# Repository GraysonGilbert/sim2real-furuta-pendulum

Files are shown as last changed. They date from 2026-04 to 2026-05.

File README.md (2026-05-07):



# **Robust Control of a Furuta Pendulum: Leveraging PPO and MuJoCo for Sim2Real Transfer**

**ENPM690 Final Project – University of Maryland**

**Team Members:**
* Grayson Gilbert

---
## Table of Contents

1. [Overview](#overview)
2. [Project Sewtup](#project-setup)
3. [Repository Layout](#repository-layout)
4. [Project Workflow](#project-workflow)
   - [Train PPO Model](#1-train-ppo-model)
   - [Evaluate Model](#2-evaluate-model)
   - [Export Policy to Header File](#3-export-policy-to-header-file)
   - [Flash Microcontroller to Run Policy on Hardware](#4-flash-microcontroller-to-run-policy-on-hardware)
5. [Hardware Components](#hardware-components)
5. [License](#license)

## **Overview**
This project bridges the gap between high-fidelity physics based simulation and physical hardware by developing a robust Proximal Policy Optimization (PPO) based controller for a furuta pendulum. The project trains an agent that can repeatedly swing up and balance a pendulum, while handling the noise, friction, and non-linearities of the real world. This was achieved through simulation using MuJoCo before being transferred to an ESP32 onboard the physical furuta pendulum. The resulting model is capable of balancing a pendulum for over an hour continuously (upper limit not found), and is robust to external input forces.

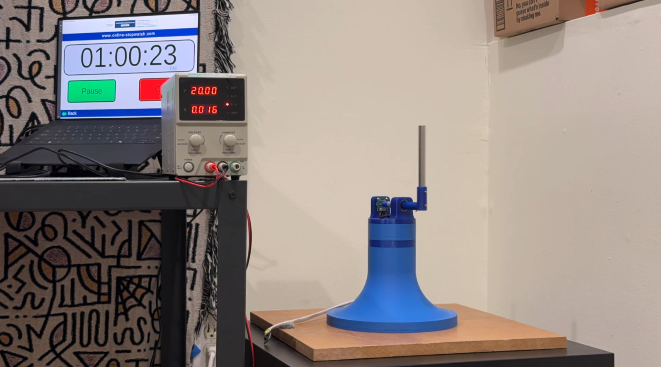
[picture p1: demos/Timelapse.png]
Description


---

## **Repository Layout**

```
sim2real-furuta_pendulum/
├── demos/                     # Project demonstration pictures and videos
├── envs/                      # Custom Gymnasium training environment
├── hardware/                  # Arduino sketch to control ESP32 and Solidworks assembly
├── rl/
│   ├── exported_models/       # Exported PPO model weight header files
│   ├── logs/                  # Model training Tensorboard logs
│   ├── saved_models/          # Automatically saved PPO models
├── sim/                    
│   ├── hw_sim_debug/          # Model and hardware related debug csv files
│   ├── meshes/                # Pendulum CAD meshes
│   ├── models/                # Pendulum MuJoCo model
├── utils/                     # All python scripts necessary for model viewing, training, evaluation, and debug
├── README.md                  # This file
├── requirements.txt           # Prerequistes
├── Dockerfile                 # Builds project docker container    
```

---
## **Project Setup**

### **Setup via Docker Container**

Download the ```Dockerfile``` from this repository and navigate to its saved location. Then run the following commands:

**Note: The docker container can be built with Nvidia GPU acceleration if the host machine has the available Nvidia hardware. This is the default configuration. If the host machine does not have the required Nvidia GPU, the Dockerfile can be modified for CPU processing only. Follow instructions inside the Dockerfile to modify the file for CPU only processing.**

#### GPU Accelerated Docker Container Setup
```shell
# Build Dockerfile image with 
docker build -t furuta-sim-env .
```

```shell
# Nvidia GPU accelerated docker container
#
# Create docker container from image [Deletes container after exit]
xhost +local:docker
docker run -it --rm \
    --gpus all \
    --device /dev/dri:/dev/dri \
    --net=host \
    -e DISPLAY=$DISPLAY \
    -v /tmp/.X11-unix:/tmp/.X11-unix \
    -v $HOME/.Xauthority:/root/.Xauthority \
    -e MUJOCO_GL=glfw \
    -e __NV_PRIME_RENDER_OFFLOAD=1 \
    -e __GLX_VENDOR_LIBRARY_NAME=nvidia \
    furuta-sim-env bash

# Nvidia GPU accelerated docker container
#
# Create docker container from image [Keeps container after exit]
xhost +local:docker
docker run -it \
    --name=mujoco-container
    --gpus all \
    --device /dev/dri:/dev/dri \
    --net=host \
    -e DISPLAY=$DISPLAY \
    -v /tmp/.X11-unix:/tmp/.X11-unix \
    -v $HOME/.Xauthority:/root/.Xauthority \
    -e MUJOCO_GL=glfw \
    -e __NV_PRIME_RENDER_OFFLOAD=1 \
    -e __GLX_VENDOR_LIBRARY_NAME=nvidia \
    furuta-sim-env bash
```

#### CPU Only Docker Container Setup:
```shell
# Buid dockerfile with
docker build -t furuta-sim-env-cpu-only .
```
```shell
### CPU only mode
xhost +local:docker
docker run -it --rm \
    --net=host \
    -e DISPLAY=$DISPLAY \
    -v /tmp/.X11-unix:/tmp/.X11-unix \
    -v $HOME/.Xauthority:/root/.Xauthority \
    -e MUJOCO_GL=glfw \
    furuta-sim-env-cpu /bin/bash
```

### **Setup via Cloning Repo**
```shell
# Clone the repository
git clone https://github.com/GraysonGilbert/sim2real-furuta-pendulum.git
```
---

## **Project Workflow**

### **1. Train PPO Model**
* The first step in the project workflow is training the PPO model to swing up and balance the pendulum. Run the following ```train.py``` script to launch the multi-core cpu based model training.

```shell
# From the sim2real-furuta-pendulum directory navigate to utils/
cd utils/
```

```shell
# Kick off training for PPO model
# 
# NOTE: The training script was designed around the Intel(R) Core(TM) Ultra 7 155H CPU.
#       It is reccomended to spread across 10 cpus cores if available. Default option
#       is set to single core training.
#
# Use --help for information about the various CLI arguments

python3 train.py --mode swing_up --num_cpus 10 # Note 10 cores specified

```

```shell
# View Tensorboard logs in a browser while training a model
#
# In a separate terminal (if running in container, terminal must be in a container as well) run the following
# from the sim2real-furuta-pendulum/ directory

tensorboard --logdir ./rl/logs/
```

### **2. Evaluate Model**

* Evaluate the results of the trained model in the MuJoCo simulation using the following ```evaluate.py``` script. This will the launch a single instance of the MuJoCo model viewer, controlled by a specified model.
```shell
# Evaluate trained policy on MuJoCo model
#
# Default values will run example simualtion on a pre-trained swing up policy
#
# Use --help for information about the various CLI arguments

 python3 evaluate.py --mode swing_up --model_name <Model name saved under /saved_models>
 
 # Example:  python3 evaluate.py --mode swing_up --model_name /swing_up_1777060502/ppo_furuta_swing_up_14000000_steps.zip
```

### **3. Export Policy to Header File**

* The next step will be to convert the resulting trained policy into source code capable of running on memory constrained devices such as an esp32. Use the following command to run a script that converts the trained PPO policy into source code.
```shell
# Export the trained policy weight into a C++ header file for running on embedded devices
#
# NOTE: The model_name argument assumes the model is within the /rl/saved_models/ direcotry
#
# Use --help for information about the various CLI arguments

python3 export_to_cpp.py --model_name <model_name_goes_here> --output <policy_name_goes_here> # Default filename is policy_net.h
```

### **4. Flash Microcontroller to Run Policy on Hardware**
* **Note: Configuring and setting up the esp32 device for use with the Arduino IDE is outside the scope of this project.**
* Move file into your local Arduino directory where libraries are stored. This will allow the ```policy_net.h``` file to be discoverable when compiling the arduino sketch. Copy over ```esp32_PPO_furuta_balancer.ino``` into an Arduino IDE for flashing onto the esp32.

---

## **Hardware Components**

* iPower GM4108h-120T Brushless Gimbal Motor
* CUI Devices AMT103V ABI Encoder
* I2C Bi-directional 3.3V-5V Level Shifter
* ESP32 Lolin Lite Development Board
* DENG FOC V3 Brushless Driver Board
* AS5047P SPI Magnetic Rotary Encoder
* 3D Printed Pendulum Parts
* 304 Stainless Steel Rods for Pendulum Mass

The full Solidworks assembly is available under the ```hardware/``` directory.

---

## **License**

This project is licensed under the **MIT License**.

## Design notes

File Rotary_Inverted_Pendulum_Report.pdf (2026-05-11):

Grayson Gilbert
ENPM690
Final Project Report

# Robust Control of a Furuta Pendulum:

## Leveraging PPO and MuJoCo for Sim2Real Transfer

## Abstract:

This project demonstrates the successful zero-shot sim2real transfer of a deep reinforcement learning policy for the robust control of a furuta pendulum. The furuta pendulum, a highly non-linear, 2-Degree of Freedom (DoF) underactuated robotic system, presents a complex continuous control challenge due to real-world friction, sensor noise, and communication latency. To effectively bridge the simulation-to-reality gap, a high-fidelity MuJoCo physics simulation was developed and meticulously calibrated against physical hardware responses using isolated drop and rotor tests. A Proximal Policy Optimization (PPO) agent was trained within a custom Gymnasium environment that utilized a multi-phase curriculum learning reward structure to sequentially teach swing-up and balancing behaviors. To ensure policy robustness upon deployment, the training environment heavily incorporated domain randomization, manual velocity noise injection, and action latency buffers. The finalized model weights were deployed directly to an ESP32 microcontroller leveraging Torque Field Oriented Control (FOC), requiring absolutely no further tuning or training on the physical hardware. The physical system successfully executed the swing-up maneuver and maintained an active balance for over a continuous hour during endurance testing. Ultimately, this work highlights the efficacy of combining accurately grounded physics simulations with robust reinforcement learning strategies to overcome the sim2real gap in complex, underactuated physical systems.

## Project Goal/Introduction:

The goal for this project is to bridge the gap between high-fidelity physics based simulation and physical hardware by developing a robust Proximal Policy Optimization (PPO) based controller for a furuta pendulum. The project aims to train an agent that can repeatedly swing up and balance a furuta pendulum, while handling the noise, friction, and non-linearities of the real world.

The furuta pendulum, also known as the rotary inverted pendulum, is a classic 2 Degrees of Freedom (DoF) underactuated control problem. It is composed of a single, powered, rotating base, attached to a free-spinning unpowered pendulum mass.

An example of a furuta pendulum controlled via classical control methods can be found by clicking the following link: Furuta Pendulum Example Video (https://youtu.be/XKzzWe15DEw?si=Pk6LUR-PZWryq1gJ)

## Literature Survey:

Proximal Policy Optimization (PPO) in Continuous Control: Deep reinforcement learning (RL) has quickly become the go-to approach for continuous control tasks in robotics. For this project, Proximal Policy Optimization (PPO) was selected because it strikes an excellent balance between sample efficiency and training stability. Research shows that PPO improves upon earlier Trust Region Policy Optimization (TRPO) methods by utilizing a clipped surrogate objective. This clipping mechanism prevents the model from making excessively large policy updates during training. As a result, it maintains performance guarantees while significantly reducing computational overhead, making it highly effective for the high-frequency 100Hz control loops required when running on the physical microcontroller.

Reinforcement Learning for the Furuta Pendulum: The Furuta pendulum is characterized by highly non-linear dynamics driven by gravity, Coriolis, and centripetal forces. Traditionally, controlling this system required complex analytical derivations and heavy simplifications of physical laws to keep the pendulum in an inverse equilibrium state. However, recent advancements demonstrate that RL algorithms can successfully bypass these explicit rigid-body modeling constraints. By allowing the agent to learn adaptive control policies directly within high-fidelity physics simulators, like MuJoCo, stable policies can be developed rapidly without the temporal or spatial constraints of training on physical hardware.

Bridging the Sim2Real Gap through Robust Control: While simulation environments allow for rapid and safe policy exploration, transferring these trained policies to the real world remains the largest hurdle. Optimal policies generated in pure simulation frequently overfit to the approximated dynamics and fail when exposed to real-world uncertainties like sensor noise, communication latency, and unmodeled friction. Robust reinforcement learning addresses this fragility by explicitly accounting for these uncertainties during the training phase. By introducing external disturbances and randomizing physical parameters (like mass, motor torque, and damping) within the training environment, the agent is forced to learn resilient recovery behaviors. This approach yields policies that are significantly more robust against physical mass changes and non-ideal actuators.

Summary and Research Implications: Overall, the literature confirms that while model-free RL algorithms like PPO are highly capable of generating successful policies for underactuated systems, raw sim-trained models are inherently brittle upon physical deployment. Overcoming this sim2real gap requires the explicit integration of robust RL techniques like domain randomization, noise injection, and structured curriculum learning. These foundational findings directly informed the methodology of this project, justifying the design of the custom Gymnasium environment to ensure the PPO agent learns predictive, robust control capable of seamless transfer to the physical system.

## Hardware:

### Component Breakdown:

- 3D Printed Pendulum Parts (base, pendulum support, and other various components)
- 1x iPower GM4108H-120T Brushless Gimbal Motor
- 1x 8mm slip ring
- 1x CUI Devices AMT103V ABI Encoder
- 1x I2C Bi-directional 3.3V-5V Level Shifter
- 1x ESP32 Lolin Lite Development Board
- 1x DENG FOC V3 Brushless Driver Board
- 1x Push-button Switch Development Board
- 1x AS5047P SPI Magnetic Rotary Encoder
- 2x 304 Stainless Steel Rods for Pendulum Mass
- 1x Benchtop Power Supply

### CAD Model:

The 3D model was originally developed using Solidworks. Each individual model was designed from scratch, except for the AS5047P encoder, which was provided by the board manufacturer. Once the individual components were complete, the entire system was assembled, and constrained accordingly. It is important to note that at this step all component frames must be aligned appropriately before exporting the model for simulation. Failure to do so will result in misaligned parts and unexpected responses from the simulated physics engine. An exploded view of the exported assembly can be found below. In an effort to simplify the model during simulation, non-essential electronic components were removed from the assembly.

Exploded View Diagram:
1. PLA Pendulum Base - bottom
2. PLA Pendulum Base - middle
3. PLA Pendulum Base - top
4. BLDC Stator
5. BLDC Rotor
6. Rotating Pendulum Support
7. Ball Bearing
8. AS5047P SPI Encoder
9. Diametric Magnet
10. Magnet Holder
11. 8mm SS Rod
12. Pendulum Rod Holder
13. 12mm SS Rod

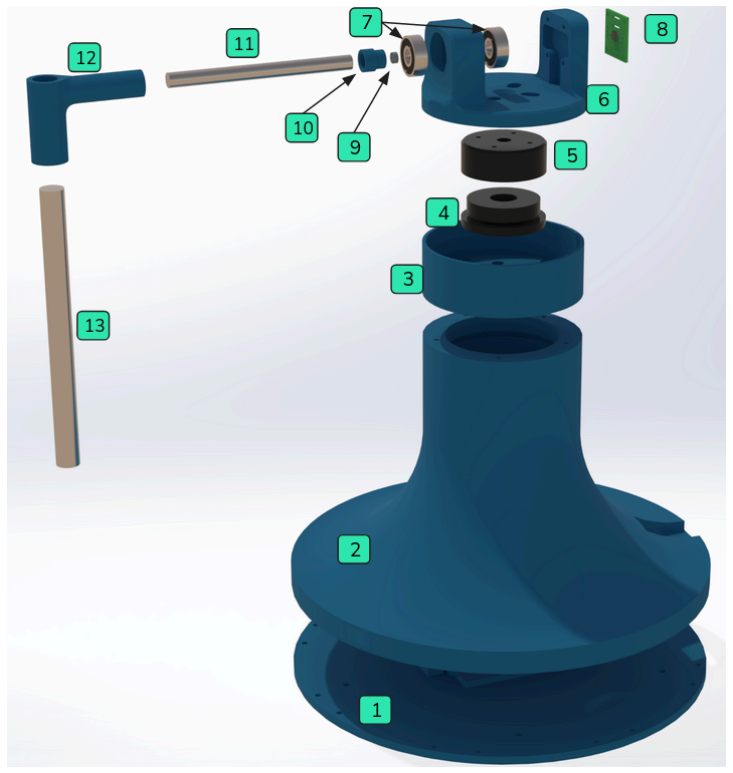
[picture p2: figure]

Exploded view of pendulum assembly.

## Model Simulation:

### Platform:

The pendulum model was then exported to the MuJoCo physics engine for simulation. MuJoCo stands for Multi-Joint Dynamics with Contact, and it is an open-source physics engine developed by Google Deepmind. MuJoCo was selected due to its performance, accuracy, and lightweight nature allowing for high-fidelity simulation on my host machine. Other notable features that aided in the selection of this platform include domain randomization during training, high-frequency training while maintaining a constant control loop rate, and mechanical fidelity between joints and components. These features allow for an accurate simulation of the furuta pendulum without the need for expensive industrial grade GPUs.

### Model Setup:

Once the Solidworks assembly was complete, it needed to be exported into a format MuJoCo can work with. Solidworks is unable to export assemblies in the MuJoCo native MJCF format, however it can export files as a URDF (Unified Robot Description Format). A python script was then developed to convert the URDF to the MJCF for processing in MuJoCo. The base model exported from Solidworks contains the 3D meshes, joints, and links necessary for simple simulation, but it lacks many of the details needed for the realistic physics based simulation.

After the base model was successfully imported into MuJoCo, system specific information was added to the model to ground the simulation in reality.

Notable motor specifications were pulled directly from the manufacturer’s website linked here. (https://shop.iflight.com/ipower-motor-gm4108h-120t-brushless-gimbal-motor-pro217)

No-load Voltage: 20V
No-load RPM: 513-567RPM [540RPM avg]
Load Voltage: 20V
Load current: 1.5A

From these specifications the following information about the motor can be calculated:

Kv (Motor Velocity Constant) = No-load RPM / No-load Voltage = 540/20 = 27
Torque constant = 8.27 / Kv = 8.27 / 27 = 0.306 Nm/A

The load current defines the control range of the actuator to [-1.5A, 1.5A], and the torque constant (0.306) is directly applied to the actuator gear value in the MuJoCo model. Additionally, position and velocity sensors at the rotor and pendulum joint were defined to replicate the physical system hardware.

After the physical motor parameters were established, the remaining simulation parameters were tuned to match the physical system response. First, an isolated pendulum drop test was performed. The rotor of the BLDC was fixed in place to completely isolate the pendulum motion. The pendulum was raised to be 90 degrees from the bottom resting position. At this point a data collection logger was started to record pendulum position over time. The pendulum was released from the horizontal position and allowed to oscillate back and forth until coming to a complete stop. The experiment was repeated in the MuJoCo simulation and the results were compared.

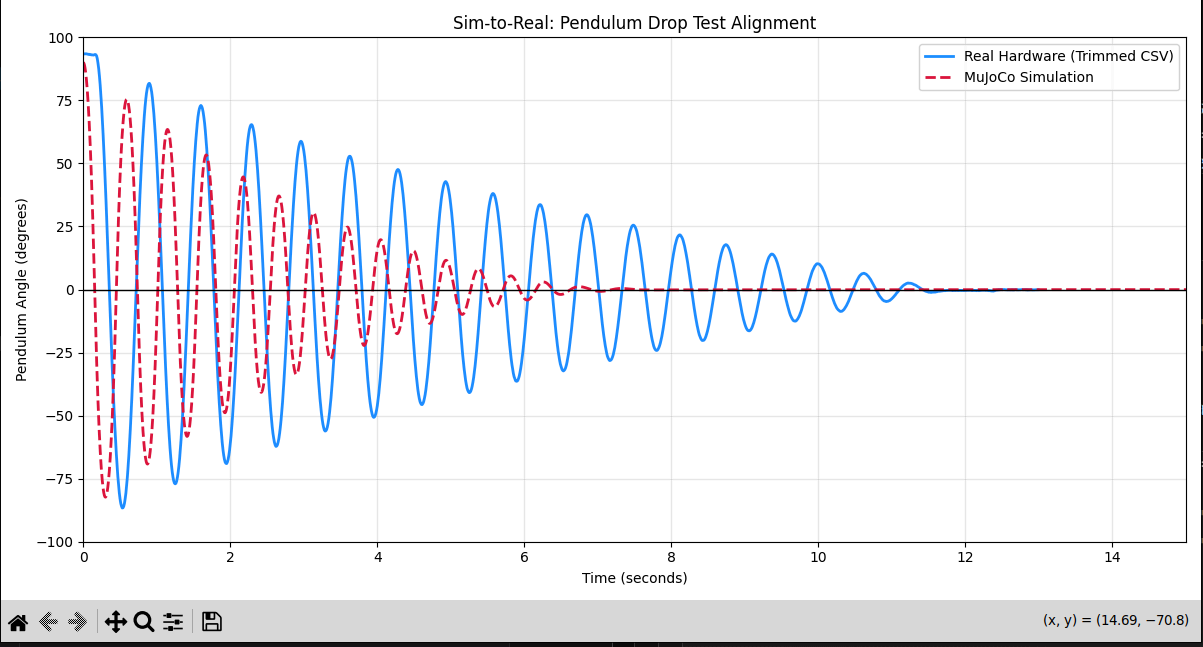
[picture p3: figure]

Initial pendulum drop test response.

The initial pendulum drop test showed that phase of the simulated pendulum oscillations did not match the physical system. This was likely due to the simulated center of gravity differing from the real system. To resolve this, I modified the pendulum center of mass location in the MuJoCo model until the phase was better aligned with the real system. The damping and friction loss parameters were also tuned until the simulated pendulum nearly matched the physical response shown below.

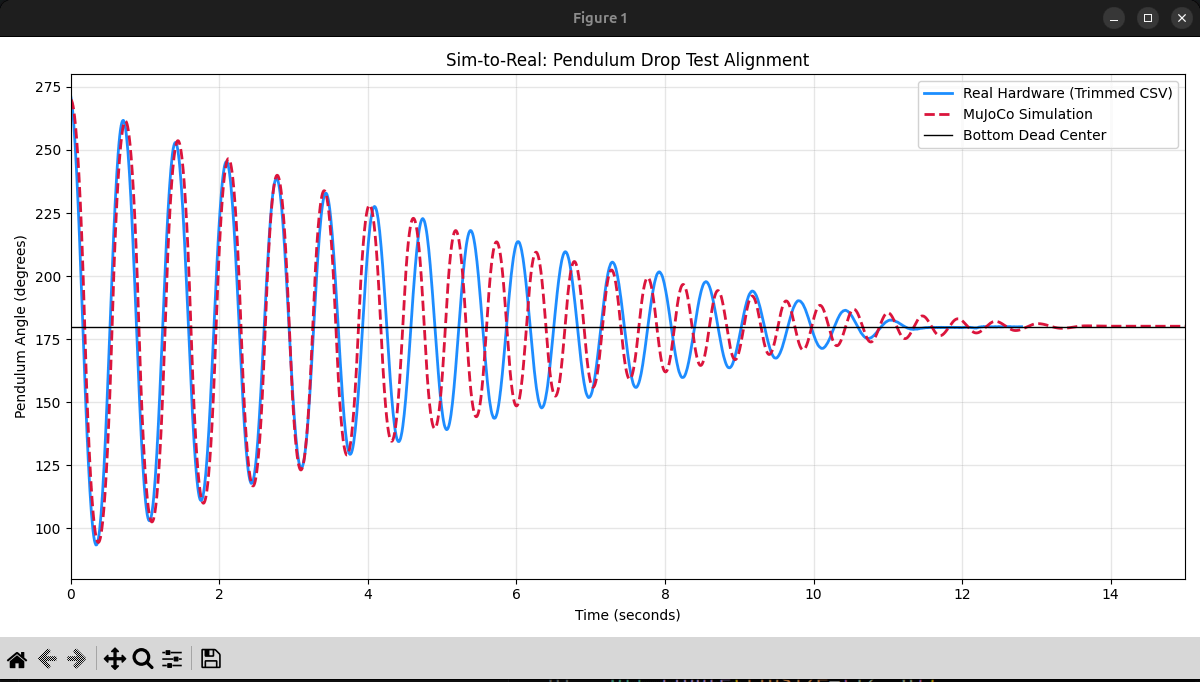
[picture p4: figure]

Final pendulum drop test response.

After the pendulum simulated response matched the physical system, the rotor isolation test was performed. For this test the pendulum was fixed in the bottom position, and the rotor was commanded to spin at constant rate. Like the first test, a logging script was deployed to record system data. The rotor isolation test started the motor from 0 rad/s and accelerated it until it reached a steady 20 rad/s. This velocity was held constant for 5 seconds before the motor commands were stopped and the rotor was allowed to coast until it came to rest. The same experiment was repeated in the simulation and the initial test results are shown below. Please note that for this initial experiment, the pendulum was not constrained appropriately resulting in noisier readings, and a different initial response than in the final tests.

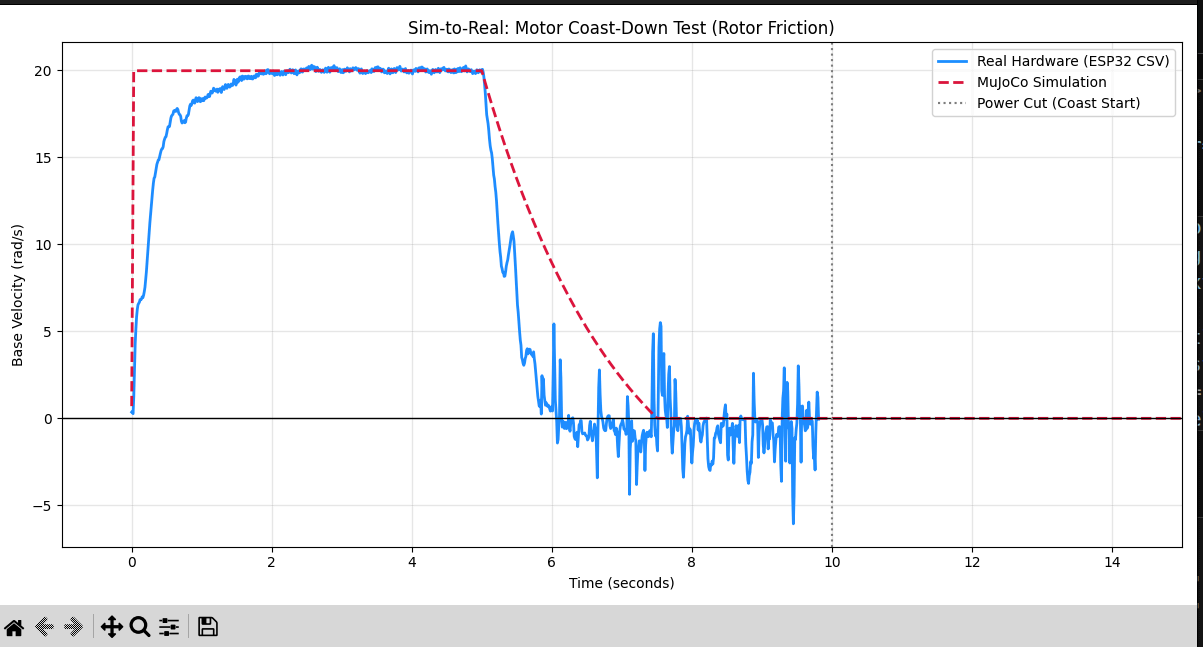
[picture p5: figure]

Initial rotor isolation test response.

After conducting the initial rotor isolation tests, the friction loss and damping values were once again tuned until the simulation better aligned with the physical system response. The final rotor isolation response is shown below.

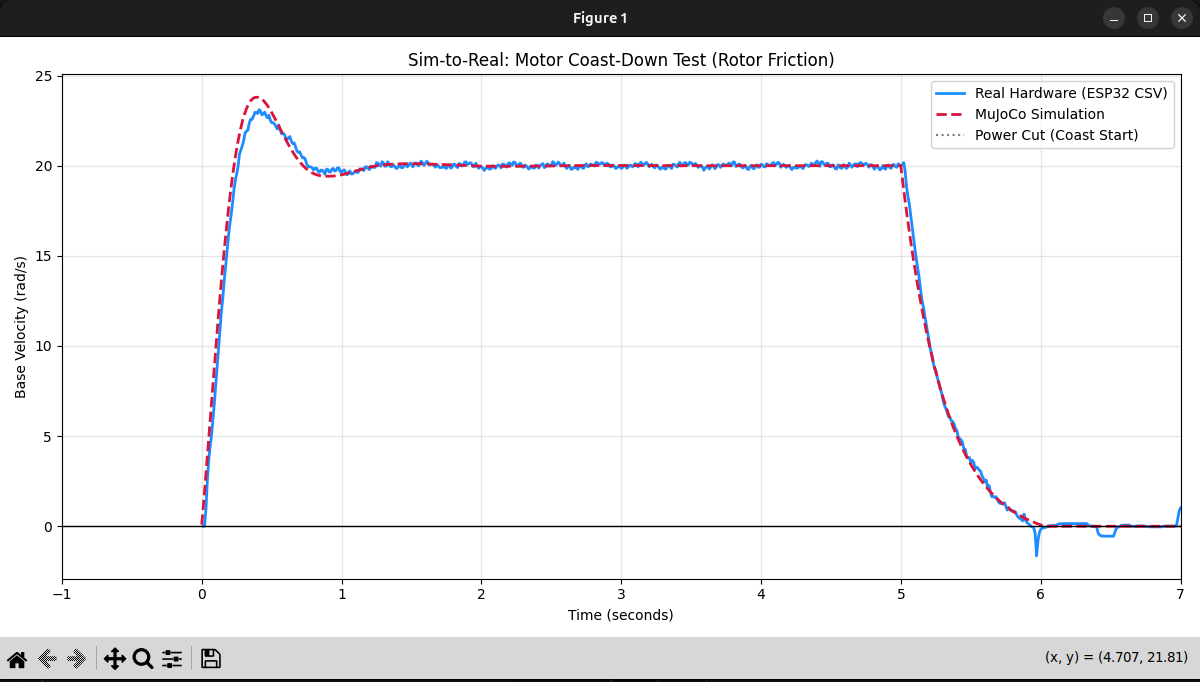
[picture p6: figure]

Final rotor isolation test response.

At this point the MuJoCo model was grounded in physics, and the simulated pendulum system response was nearly identical to the physical pendulum system. The model was now ready for the next step, which was creating the environment for training.

### Environment Setup:

With the MuJoCo model ready for training, the next step was to create the simulation environment for reinforcement learning. To achieve this, I wrapped the MuJoCo model in a custom Gymnasium environment. Gymnasium is a reinforcement learning API that bridges the gap between the MuJoCo physics engine and the RL algorithm. The environment consists of the following functions: initialize, step, observe, terminate, reset, and reward.

Initialize:
The environment initializes by first loading in the MuJoCo model data. After this, it will define a frame skip variable and set it equal to 10. The frame skip is used to mimic the real world 100Hz control loop that runs on the microcontroller. A frame skip of 10 results in a control loop rate of 100Hz because the MuJoCo model timestep is 0.001 seconds. After the frame skip is defined, physical hardware limits like motor current and encoder resolution are set. Then the 1 dimensional action space is initialized and constrained to the range of [-1, 1]. For this environment, the action space is the commanded motor current. Next, the 6 dimensional observation space is defined and constrained to the range of [-1, 1]. Various model parameters like motor torque constant, model damping, model friction, and model mass are then initialized for future domain randomization in the reset function. Finally, the action delay buffer is initialized to mimic real life communication latency.

Step:
This function is also known as the execution loop for the RL environment. The simulation step takes the model action as a parameter, in this case the commanded motor current. Because the action is constrained to a range of [-1, 1], it is multiplied by the maximum motor current to scale the action into physical amps. Next the action is added to the delay buffer so it does not get applied immediately. Instead the model must wait a couple steps before the action is applied. This buffer mimics the real life communication latency in the system, and forces the model to learn predictive control instead of relying on instantaneous response times. Then, the commanded current for this given step is applied for the next 10 frames. This is how the frame skip is implemented, and sets the 100Hz control rate. After the frame skips are complete, the raw position and velocity data for the motor and pendulum are read from the model. The pendulum position is then wrapped between the values of [-pi, pi], and the raw system state is generated. The observation function is called using this raw state as an input, followed by the reward function. Next, the previous target current is updated to be the current target current, and the termination function is checked to see if termination criteria are met. If the simulation is to be terminated, the type of termination is logged for telemetry. Finally, the observation, reward, termination, and telemetry values are returned.

Observation:
The observation function takes the raw system state as an input parameter. The raw state includes rotor position, rotor velocity, wrapped pendulum position, and pendulum velocity. Then the raw state positions are quantized into acceptable values within the encoder resolution. Next, noise is manually injected into the velocity sensor readings. This noise is added because of the way the physical system calculates the pendulum and rotor velocity. In the real system, the velocity is calculated by taking the derivative of the encoder position. These sensor readings are inherently noisy, which can have a large impact on overall velocity when the motor or pendulum is moving at slow speeds. The simulation sensors do not automatically have noise in their readings, so it must be injected manually. Next the maximum rotor position, maximum rotor velocity, and maximum pendulum velocity are defined. These values are used in the following observation array to keep the velocity and position values between the range [-1, 1]. The observation space array includes the following values:
1. Discrete rotor position / maximum rotor positon
2. Noisy rotor velocity / maximum rotor velocity
3. Sine component of discrete pendulum position
4. Cosine component of discrete pendulum position
5. Noisy pendulum velocity / maximum pendulum velocity
6. Previous commanded current / maximum commanded current

The pendulum position is broken down in its sine and cosine components as a way to prevent sudden value jumps when the pendulum wraps around the maximum position. These sudden jumps in value would otherwise confuse the RL model during training, resulting in poor performance.

Reset:
The simulation reset occurs when training starts, or when termination criteria are met. The reset function completely resets the training environment, preparing it for the next episode of training. The pendulum environment contains two potential training modes that affect the system reset. The training modes are Balance and Swing Up. The Balance mode resets the pendulum environment and initializes the pendulum near the Top Dead Center (TDC) position. This is the upright, unstable position. The Swing Up mode resets the pendulum environment and initializes the pendulum in the Bottom Dead Center (BDC) position. Both training modes also incorporate domain randomization. This means that the simulation randomizes the values for motor torque, model friction, model damping, and model mass within a specified range. This domain randomization helps to improve overall model performance and robustness.

The various training modes are a result of curriculum learning. For more information about the curriculum learning process please see the Reward function section below.

Termination:
The termination criteria for the simulation episode is based on the mode of the training being conducted. If any of these criteria are met during a training episode, the simulation will immediately stop the episode, log the termination type, and reset the environment.

The termination criteria for the Balance training mode is the following:
- The pendulum drops below 15 degrees away from the TDC position
- The motor spins more than 2 full rotations in any one direction

The termination criteria for the Swing Up training mode is the following:
- The motor spins more than 2 full rotations in any one direction

Reward:
The reward function is the most important part of the training environment. Without an appropriately designed reward, the model will not be able to learn the desired task. Swinging the pendulum from the BDC position, and then catching and balancing it in the TDC position is not trivial. It would be very difficult to design a reward function that can achieve this system response without breaking it up into smaller parts. This is where curriculum learning comes into play. Instead of starting model training by attempting difficult and complex tasks, the curriculum learning approach breaks the complex problem down into smaller more manageable tasks. The agent is taught to successfully complete the smaller, easier tasks before learning more challenging operations. This approach is very similar to how students first learn basic arithmetic before tackling harder concepts like calculus.

With this in mind, the pendulum problem was broken down into two main sub-tasks: 1. Swing up the pendulum 2. Catch and balance the pendulum. The second task was the easier of the two so that is where the training started. The model learned to stabilize the pendulum in the upright position using the Balance training mode. Each episode reset the pendulum near the TDC position allowing for the model to have millions of opportunities to learn to balance the unstable mass. Once the reward was designed in a way that enabled the model to successfully balance the pendulum, the swing up task was taught. The swing up task was trained using the Swing Up mode. It built upon the current reward structure to successfully generate momentum to swing the pendulum from the BDC position up to TDC and balance it there for extended periods of time. The final reward function was broken down into two distinct phases based on pendulum position with a third transition phase blending everything together.

The overall reward function is made up of a variety of rewards, bonuses, and penalties. A high level overview of all the rewards, bonuses, and penalties are as follows:

- Upright reward = cos( pendulum position ) - 1
- Effort penalty = 0.001 * ( current ** 2 )
- Centering penalty = 0.03 * ( rotor position ** 2 )
- Action rate penalty = 0.5 * ( ( current -previous current ) ** 2 )
- Rotor velocity penalty = 0.05 * ( rotor velocity ** 2 )
- Catch velocity penalty = 0.02 * ( pendulum velocity ** 2 ) + 0.05 * ( rotor velocity ** 2 )
- Momentum bonus = 0.1 * abs( pend. Velocity ), values clipped between [0.0, 0.8]
- Swing weight = 1.0 - catch weight
- Blended Momentum Bonus = momentum bonus * swing weight
- Blended Velocity Penalty = ( swing base velocity penalty * swing weight ) - ( catch velocity penalty * catch weight )
- Catch Bonus = 3.0 if catch weight == 1.0, otherwise 0
- Duration Bonus = 0.01 * consecutive upright steps

The total reward is defined at the sum of all rewards and bonuses minus the sum of all penalties.

Swing Up Phase Reward Structure:
In the Swing Up phase, reward structure promotes generating pendulum momentum, in order to eventually swing the pendulum up to the TDC position. The pendulum is in the phase any time the pendulum position is greater than 0.6 rads away from TDC. The Swing Up phase reward structure is the following:
- Catch weight = 0
- Swing weight = 1
- Blended momentum bonus -> has full momentum bonus effect
- Blended velocity penalty -> only swing base velocity penalty, no catch penalties
- Catch bonus = 0

- Consecutive upright steps = 0
- Duration bonus = 0

Transition Phase Reward Structure:
The distance between 0.6 rads away from TDC and 0.2 rad away from TDC is considered the transition phase of the reward structure. This space is where both the Swing Up and Balance phases blend together to smoothly transition from one reward structure to the next. The transition phase also helps to slow down the pendulum momentum generated in the Swing Up phase so the pendulum does not carry over the TDC position and swing back towards the BDC position. The transition phase reward structure is as follows:
- Catch weight = (1.2 - distance from TDC) / 1
- Swing weight = less than 1
- Blended momentum bonus -> has reduced momentum bonus effect
- Blended velocity penalty -> contains some swing base velocity penalty and some catch penalties
- Catch bonus = 0
- Consecutive upright steps = 0
- Duration bonus = 0

Catch and Balance Phase Reward Structure:
When the pendulum position is less than 0.2 rads from TDC the Catch and Balance reward phase kicks in. Here the reward heavily promotes keeping the pendulum in this upright position as close to TDC as possible. The Catch and Balance reward structure is as follows:
- Catch weight = 1
- Swing weight = 0
- Blended momentum bonus = 0
- Blended velocity penalty -> swing base velocity penalty + catch velocity penalty
- Catch bonus = 3
- Consecutive upright steps -> +1 for each consecutive step in this phase
- Duration bonus -> greater than 0, and increasing
These different phases of a single reward function allow for one model to be able to learn multiple unique tasks in order to achieve the goal of swinging up, catching, and balancing the pendulum in an unstable position.

Logging:
Throughout the entire simulation process, the observation space of the simulated pendulum is logged. This allows for detailed evaluation and comparison of the simulated and physical pendulum system.

## Reinforcement Learning:

### Algorithm/Approach:

The control strategy relies on Proximal Policy Optimization (PPO), a stochastic policy gradient method chosen for its balance of sample efficiency and stability in continuous action spaces. The overall training pipeline is divided into three distinct phases to maximize the likelihood of success when transferring to real hardware: 1. Initial policy optimization using PPO 2. Improving robustness through randomization 3. Hardware deployment and validation.

The Initial policy optimization using PPO is where the model will learn to swing up and balance the pendulum, with a reward function that promotes smooth motor torque and extended pendulum balance times. The second phase is where the model will incorporate noise into the sensors, latency in motor response time, and changes in physical constants such as mass , motor torque, damping, and friction. This will force the model to create a control response that can withstand the randomness that is the real world. The final phase will be deploying the model on the hardware and validating its effectiveness through balancing the pendulum.

### Training Architecture:

The training program leverages Stable Baseline 3, an open-source python library that provides reliable implementations of the Deep Reinforcement Learning algorithms using the PyTorch framework. More specifically, the training program uses the PPO model built into SB3. The training can be initialized using one of two modes, the Balance mode or the Swing Up mode. Each mode corresponds to the initial environment conditions described in the custom gymnasium environment above. When training is initialized, it will start 10 parallel processing instances of the pendulum model. Parallelizing the model training enables significantly more training capacity without increasing overall training time. The training program also leverages SB3’s extensive logging capabilities with Tensorboard. In addition to the built in logging features, a custom termination callback was implemented to track the number of each termination type as the training evolves. These logging features allow for model evaluation without seeing the simulated system response of the pendulum model. For periodic model evaluation, the training program saves checkpoint policies every 10,000,000 steps to get a better understanding of how the agent is learning without stopping training completely. A single training episode can have a maximum of 1000 timesteps before restarting. This helps to prevent the model from wasting time learning ineffective strategies. The training will proceed for a total of 30,000,000 steps split amongst all parallel instances before saving the final model policy.

Model Hyperparameters:
- Learning rate: 0.0003
- Number steps: 2048

- Batch size: 2048
- Number epochs: 10
- Entropy coefficient: 0.03
- Clip range: 0.2

## Simulation Results:

Following the completion of model training on the pendulum simulation, the model was able to successfully swing up and balance the pendulum in the TDC position. A recording of the simulation in action can be found below:

Simulation Demonstration (https://drive.google.com/file/d/1TTlGVXxSfAPoyIrrarF8xxBkDhk0gaSO/view?usp=sharing)

Below are screenshots of the Tensorboard logs saved from the simulation training process. The first 4 charts are the logs that were most frequently used when evaluating the success of a model during training. Starting from the top left, the base drift termination chart plots how frequently the simulation ended prematurely due to the base drift termination criteria. The next chart shows the pendulum drop criteria. The Swing Up training mode was performed for this simulation, so pendulum drop criteria is ignored. The next chart shows the average reward of a simulation. The reward initially started out very negative as the pendulum was heavily penalized for improper control of the pendulum. As the model learned to generate momentum to swing the pendulum, the reward function slowly increased until it reached 0. When the model finally caught and balanced the pendulum for the first time, the reward sharply increased to the +6000 range where it remained for the rest of the simulation. The top right chart shows the average length of a simulation episode. Each episode can have a maximum of 1000 timesteps before termination. A successful simulation should be able to reach the maximum simulation timestep without terminating. As you can see, this simulation approached the maximum 1000 timestep limit once the model learned to balance the pendulum successfully.

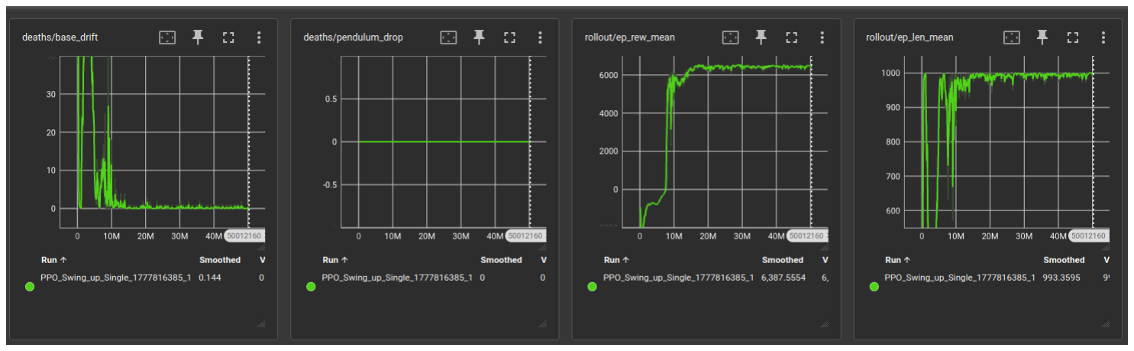
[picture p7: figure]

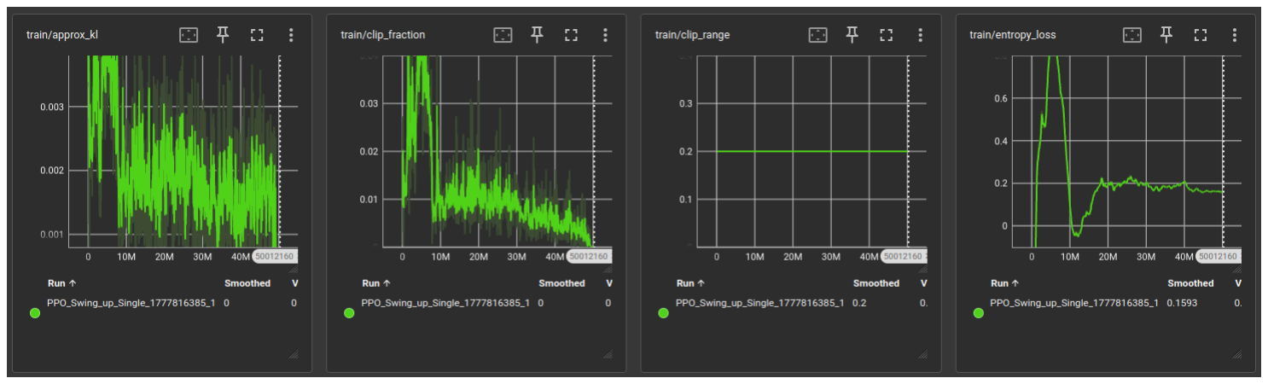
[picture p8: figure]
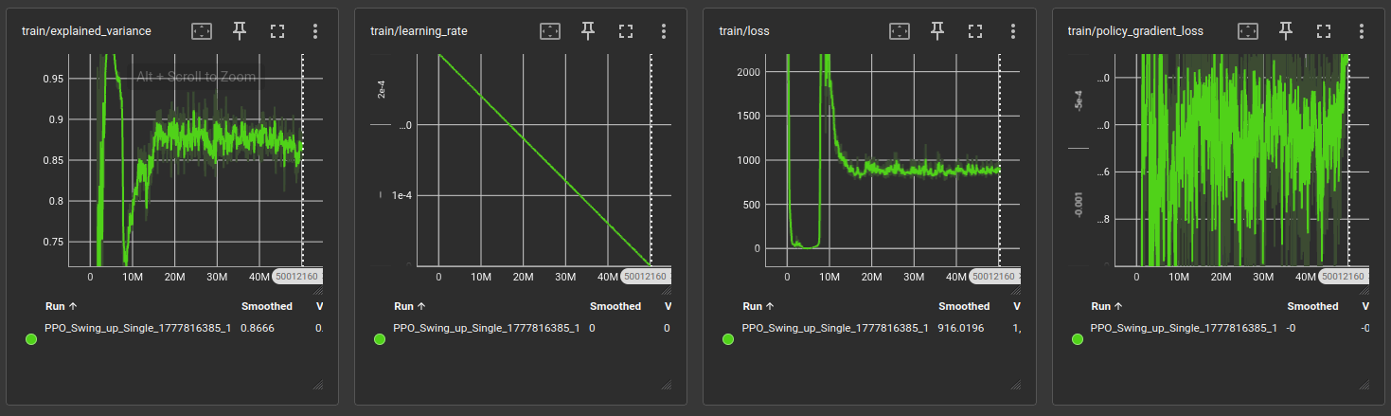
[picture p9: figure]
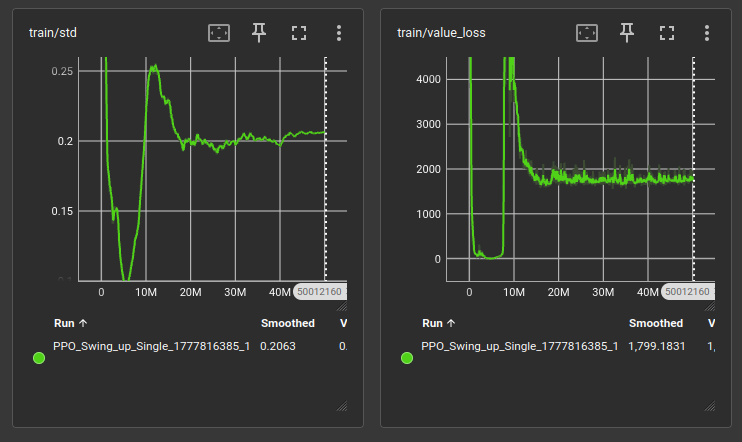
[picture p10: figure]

Tensorboard logging charts for model evaluation.

## Embedded Software:

### Software Architecture:

Once the simulation was successful, the process of transitioning the model onto an embedded device could take place. A completed simulation outputs the trained model in a zip file containing JSON data files, PyTorch variable files, policy files, and policy optimizer files. This zip file cannot directly run on an embedded device. Instead the trained policy weights needed to be exported into a C++ header file, so they can be compiled into the machine code running on the ESP32.

The embedded software architecture utilized both processing cores in the ESP32 microcontroller. Core 0 handled all RL processing related tasks. This core read in the pendulum observation space and calculated the required target current using the exported model weights. This control loop was fixed at the planned 100Hz rate to ensure that the commanded current was received when the model expected it. Core 1 handled all the motor control commands. The brushless motor that drives the pendulum system is controlled using Torque Field Oriented Control (FOC) via current sensing. FOC is a high performance control technique for driving Brushless DC motors (BLDC). It allows the motor to be controlled with extreme precision. The FOC control code leverages the open-source library Simple-FOC for the algorithm implementation as well as ESP32 specific firmware drivers. Getting into the weeds of the FOC control algorithm is outside the scope of this project.

### Logging and Debug:

During the first system startup, the pendulum, surprisingly, did not work. In an attempt to understand what was wrong in the embedded software, observation space logging was implemented. Because the ESP32 has limited memory, the log information was recorded and sent over the serial line. As the system continuously failed to balance the pendulum, a python script was listening on the ESP32 COM port and recording the messages into a .csv file. The physical system observation space could then be compared to the simulated observation space to determine where it all falls apart.

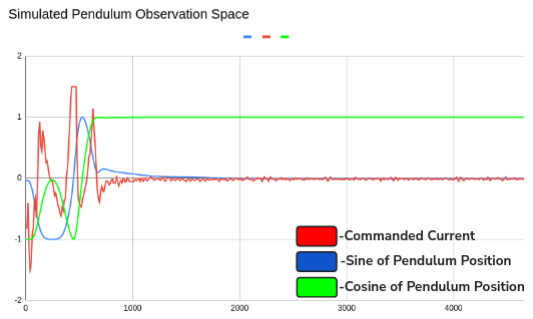
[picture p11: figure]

Simulated pendulum observation space.

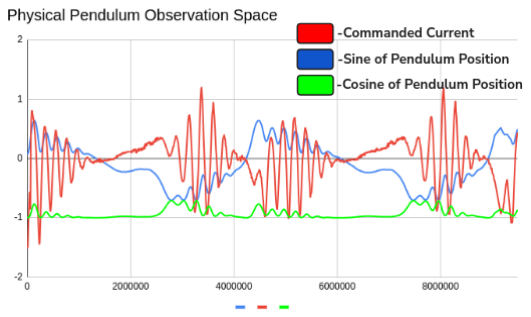
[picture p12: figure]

Physical pendulum observation space.

When comparing the physical system observation space against the simulated system observation space, it became clear that the physical system commanded current (red line) would drive the sine of the pendulum position (blue line) in the wrong direction. This was caused by an inversion in the pendulum encoder installed on the physical system. This inversion was quickly remedied with a sign change in the embedded code, but it is a great reminder why detailed logging is important in physical systems. The rich debugging tools available in simulation are not always available in real hardware.

## Sim2Real Transfer Results:

Once all the bugs in the embedded software were resolved, the model was able to successfully transfer from simulation to physical hardware without any further tuning or training. The goal of the project was achieved and the simulation to reality gap was successfully crossed. Video demonstrations of the physical pendulum balancing can be found below.

Physical Pendulum Demonstration (https://drive.google.com/file/d/1rAuRg7YcpLDl3BJN6BurSswluA5AqTLE/view?usp=sharing)

Additionally, the upper limits of the pendulum control model were challenged with an endurance test. To achieve this, a timelapse video was set up to record the pendulum balancing with a stopwatch playing in the background. The goal was to see how long the pendulum could balance before it fell over. After 1 hour of continuous balancing, the pendulum had still not fallen. At this point the challenge was considered a success, and the system was powered off. The results show that the pendulum can certainly balance for at least 1 hour without dropping the pendulum, however it is likely that the pendulum can balance for well over one hour. A timelapse video showcasing the challenge is linked below.

1 Hour Endurance Test (https://drive.google.com/file/d/1mQCUv2D7nZcvLgrq_ALu-NTPiUjCYTR0/view?usp=sharing)

## Contribution:

Key repositories used in this project are:
- MuJoCo
- Gymnasium
- Stable Baseline 3
- Numpy
- Imageio
- Pandas
- Matplotlib
- Arduino Libraries:
- Simple FOC
- Simple FOC Drivers
- ESP32HWEncoder
- SPI
- AS5047P

Without the open source projects listed above, this project would not have been possible. This project is licensed under the MIT license, allowing anyone to access and build on the work I have started.

My own personal contributions for this project involve the following:
- Designed 3D model of furuta pendulum system in Soldiworks
- 3D printed pendulum model, and prototyped physical system
- Developed and soldered pendulum electrical control circuit involving ESP32, buttons, encoders, and brushless motor
- Designed MuJoCo system model for simulating virtual pendulum system
- Calibrated MuJoCo through numerous physical system experiments
- Developed custom Gymnasium environment to perform reinforcement learning training with MuJoCo model
- The training environment included custom termination, observation, reset, step, and reward functions
- Leveraged Stable Baseline 3 to develop a training formula for agent learning
- Developed various helper scripts to convert files to useable formats, compare simulated and physical test data, evaluate trained models, and more
- Developed embedded software to run trained model on the microcontroller and control brushless motor using Field Oriented Control techniques
- Flashed microcontroller and debugged physical system ultimately achieving the project goal of successful simulation to reality transfer enabling the control of a furuta pendulum via RL model

## Conclusion:

In conclusion, this project successfully bridged the gap between high-fidelity physics simulation and physical hardware by developing a robust Proximal Policy Optimization (PPO) controller for a Furuta pendulum. By meticulously calibrating a MuJoCo simulation to match the real-world dynamics of the system and incorporating domain randomization, the trained agent achieved seamless sim2real transfer without requiring further hardware tuning. A significant contribution of this work lies in the development of a custom Gymnasium environment that leveraged curriculum learning to effectively break down the complex control problem into manageable swing-up and balance sub-tasks. Furthermore, the deployment of this reinforcement learning model on an ESP32 microcontroller utilizing Torque Field Oriented Control (FOC) resulted in highly stable physical performance, demonstrated by the system's ability to balance continuously for over an hour. While the study successfully mitigated physical constraints like sensor noise and communication latency through proactive simulation modeling, future research could focus on optimizing the embedded software architecture to better accommodate microcontrollers with limited memory or expanding the curriculum learning framework to other complex underactuated robotic systems. Ultimately, by releasing the project under an open-source MIT license, this work provides a verified, accessible foundation for future advancements in reinforcement learning and applied robotics.

## References:

### Papers:

Hong, M. R., Kang, S., Lee, J., Seo, S., Han, S., Koh, J.-S., & Kang, D. (2023). Optimizing reinforcement learning control model in Furuta pendulum and transferring it to real-world. IEEE Access, 11, 95195–95200.

Lutter, M., Mannor, S., Peters, J., Fox, D., & Garg, A. (2021). Robust value iteration for continuous control tasks. Robotics: Science and Systems XVII.

Meng, W., Zheng, Q., Pan, G., & Yin, Y. (2023). Off-policy proximal policy optimization. Proceedings of the AAAI Conference on Artificial Intelligence, 37(8), 9162–9170.

Moos, J., Hansel, K., Abdulsamad, H., Stark, S., Clever, D., & Peters, J. (2022). Robust reinforcement learning: A review of foundations and recent advances. Machine Learning and Knowledge Extraction, 4(1), 276–315.

Wang, Y., He, H., Tan, X., & Gan, Y. (2019). Trust region-guided proximal policy optimization. arXiv.

### Websites (Project Dependencies):

GM4108H-120T Gimbal Motor: https://shop.iflight.com/ipower-motor-gm4108h-120t-brushless-gimbal-motor-pro217

Simple FOC Project: https://simplefoc.com/
MuJoCo Project: https://github.com/google-deepmind/mujoco
Gymnasium Project: https://gymnasium.farama.org/index.html
Stable Baseline 3 Project: https://stable-baselines3.readthedocs.io/en/master/index.html Imageio Project: https://imageio.readthedocs.io/en/stable/#
Pandas Project: https://pandas.pydata.org/
MatPlotLib Project: https://matplotlib.org/
Numpy Project: https://numpy.org/
Arduino Project: https://www.arduino.cc/

### Videos:

Furuta Pendulum Example Video: https://youtu.be/XKzzWe15DEw?si=Pk6LUR-PZWryq1gJ

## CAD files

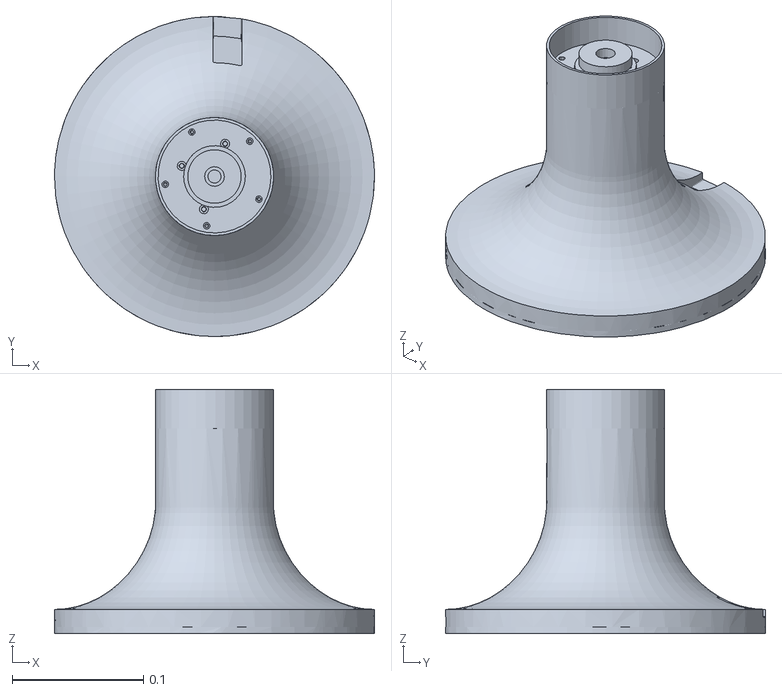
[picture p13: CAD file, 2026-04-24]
sim/meshes/base_link.STL
0.244 x 0.244 x 0.186

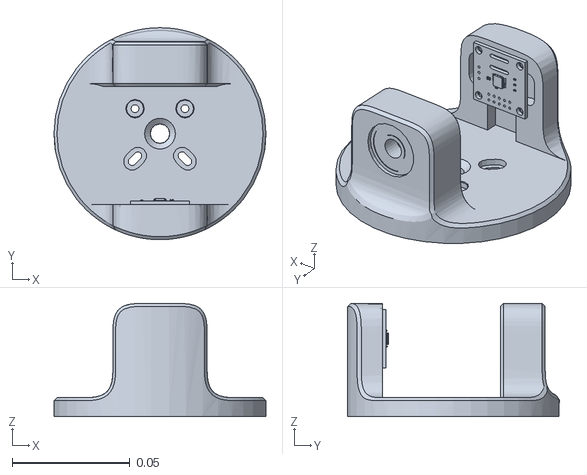
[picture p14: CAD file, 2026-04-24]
sim/meshes/rotating_base_link.STL
0.09 x 0.0898 x 0.048

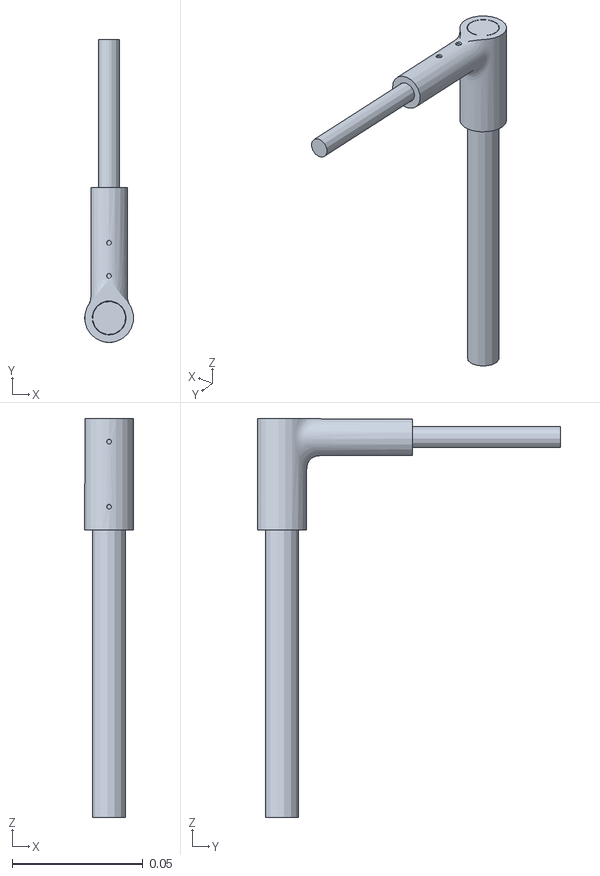
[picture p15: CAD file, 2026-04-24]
sim/meshes/pendulum_link.STL
0.0186 x 0.116 x 0.152

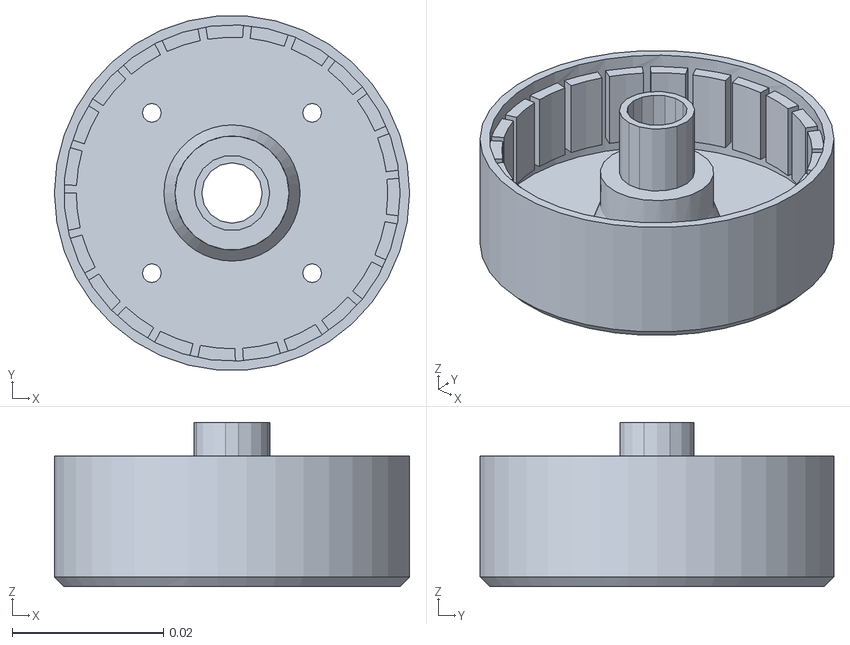
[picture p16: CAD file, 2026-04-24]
sim/meshes/rotor_link.STL
0.047 x 0.0468 x 0.0217

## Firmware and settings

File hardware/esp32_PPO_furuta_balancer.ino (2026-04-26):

#include <SimpleFOC.h>
#include <SimpleFOCDrivers.h>
#include <encoders/esp32hwencoder/ESP32HWEncoder.h>
#include <SPI.h>
#include <AS5047P.h>
#include "driver/pcnt.h"
#include "policy_net.h" // Exported Trained Model


// BLDC Hardware Defintions:
ESP32HWEncoder bldc_encoder = ESP32HWEncoder(32, 33, 2048);
BLDCDriver3PWM driver = BLDCDriver3PWM(27, 26, 14, 12);
BLDCMotor motor = BLDCMotor(11);
InlineCurrentSense current_sense = InlineCurrentSense(0.01f, 50.0f, 34, 35);

// SPI Encoder Definition:
#define SLAVE_SELECT_PIN 5
AS5047P pend_encoder(SLAVE_SELECT_PIN, 10000000);
float pend_angle_offset = 0.0f;

// Low pass filter to reduce encoder noise
LowPassFilter lpf_pend_vel = LowPassFilter(0.005f);

// Safety Button Definition:
const int BUTTON_PIN = 13;

// Inter-core shared memory:
volatile float shared_target_current = 0.0f;
volatile bool is_estopped = false; // Temporarily stop motor
volatile bool hard_lockout = false; // Permanently stop motor
float prev_current_cmd = 0.0f; // Previous applied current

// Logging struct:
typedef struct {
  uint32_t timestamp;
  float obs[6];
  float action;
} LogFrame;

// Queue Handle
QueueHandle_t logQueue;

// --- BACKGROUND LOGGING TASK (Runs on Core 0, Low Priority) ---
void loggingTask(void * pvParameters) {
  LogFrame frame;
  
  // Print a CSV header
  Serial.println("Time_ms,Obs0,Obs1,Obs2,Obs3,Obs4,Obs5,Action");

  for(;;) {
    // Wait for data to appear in the queue. 
    if ( xQueueReceive(logQueue, &frame, portMAX_DELAY) == pdPASS ) {
      
      // Print the frame as a CSV line. 
      Serial.printf("%lu,%.4f,%.4f,%.4f,%.4f,%.4f,%.4f,%.4f\n", 
                    frame.timestamp, 
                    frame.obs[0], frame.obs[1], frame.obs[2], 
                    frame.obs[3], frame.obs[4], frame.obs[5], 
                    frame.action);
    }
  }
}

// Helper function for angle wrapping between [-pi, pi]
float wrap_angle(float angle)
{
  float wrapped = fmod(angle + PI, 2.0f * PI);
  if( wrapped < 0 )
  {
    wrapped += 2.0f * PI;
  }
  return wrapped - PI;
}

void encoder_cal(AS5047P encoder)
{
  Serial.println("Running pendulum encoder calibration...");
  delay(1000);

  float sum_sin = 0.0f;
  float sum_cos = 0.0f;
  const int num_samples = 100;

  for( int i = 0; i < num_samples; i++)
  {
    float raw_rad = encoder.readAngleDegree() * (PI / 180.0f);
    sum_sin += sin(raw_rad);
    sum_cos += cos(raw_rad);

    delay(2);
  }

  float avg_raw_angle = atan2(sum_sin, sum_cos) * (180.0f / PI);
  if( avg_raw_angle < 0 )
  {
    avg_raw_angle += 360.0f;
  }

  pend_angle_offset = 180.0f + avg_raw_angle;
  Serial.printf("Calibration complete. Rest angle: %.2f deg, Offset applied %.2f\n", avg_raw_angle, pend_angle_offset);
}

// Core 0: RL and Safety Tasks:
void core0_task(void * pvParameters)
{

  TickType_t xLastWakeTime = xTaskGetTickCount();
  const TickType_t xFrequency = pdMS_TO_TICKS(10);

  // Safety Button Variables:
  uint8_t click_count = 0;
  uint32_t last_press_time = 0;
  bool last_button_state = HIGH; // Input pullup to high

  const uint32_t CLICK_WINDOW = 800;
  const uint32_t DEBOUNCE_DELAY = 50;

  // Velocity Tracking Variables:
  float prev_pend_pos = 0.0f;
  uint32_t prev_time_us = micros();

  for( ;; )
  {
    // -------------------- Safety Button Logic --------------------
    uint32_t now = millis();
    bool current_button_state = digitalRead(BUTTON_PIN);

    if( current_button_state == LOW && last_button_state == HIGH )
    {
      if( now - last_press_time > DEBOUNCE_DELAY )
      {
        if( now - last_press_time <=  CLICK_WINDOW )
        {
          click_count++;
        }
        else
        {
          click_count = 1; // Press too slow, reset click count
        }
        last_press_time = now; // Update timestamp
      }
      if( click_count >= 3 )
      {
        hard_lockout = true;
        Serial.println("SAFETY LOCK OUT ENABLED!");
      }
    }
    last_button_state = current_button_state;
    // ----------------- End of Safety Button Logic -----------------

    // Read Pendulum Position and Compute Velocity:
    float angle_deg = pend_encoder.readAngleDegree() + pend_angle_offset;
    uint16_t magnitude = pend_encoder.readMagnitude();

    float pend_pos = -(angle_deg * (PI / 180.0f));

    uint32_t now_us = micros();
    float dt = (now_us - prev_time_us) * 1e-6f;

    if( dt <= 0.0f ) // Divide by zero check
    {
      dt = 0.0001f;
    }

    float delta_angle = wrap_angle(pend_pos - prev_pend_pos);
    float raw_pend_vel = delta_angle / dt;
    float pend_vel = lpf_pend_vel(raw_pend_vel);

    prev_pend_pos = pend_pos;
    prev_time_us = now_us;

    // Encoder Magnitude Check:
    bool magnet_fault = (magnitude < 2000);
    if( magnet_fault )
    {
      Serial.println(">> FAULT: Magnet magnitude too weak!");
    }

    // Check Safety Button State
    if( current_button_state == LOW || hard_lockout )
    {
      is_estopped = true;
      shared_target_current = 0.0f;
    }
    else
    {
      is_estopped = false;
    }
   
    // Format Observations and Run RL Model:
    float rotor_pos = motor.shaft_angle;
    float rotor_vel = motor.shaft_velocity;
    float pend_pos_wrapped = wrap_angle(pend_pos);

    float obs[6];
    obs[0] = constrain(rotor_pos / (4.0f * PI), -1.0f, 1.0f);
    obs[1] = constrain(rotor_vel / 50.0f, -1.0f, 1.0f);
    obs[2] = sin(pend_pos_wrapped);
    obs[3] = cos(pend_pos_wrapped);
    obs[4] = constrain(pend_vel / 50.0f, -1.0f, 1.0f);
    obs[5] = prev_current_cmd / 1.5f;

    if( !is_estopped )
    {
      float raw_action[1];
      compute_action(obs, raw_action);

      float calculated_target = constrain(raw_action[0], -1.0f, 1.0f) * 1.5f;
      prev_current_cmd = calculated_target;
      shared_target_current = calculated_target;

      // // SHADOW MODE TEST:
      // shared_target_current = 0.0f;

      // Serial.print(pend_pos);
      // Serial.print(",");
      // Serial.print(pend_pos_wrapped);
      // Serial.print(",");
      // Serial.println(calculated_target);

      LogFrame current_frame;
      current_frame.timestamp = now_us;
      memcpy(current_frame.obs, obs, sizeof(obs));
      current_frame.action = calculated_target;

      xQueueSend(logQueue, &current_frame, 0);

    }
    else
    {
      shared_target_current = 0.0f;
      prev_current_cmd = 0.0f;
    }
 
    vTaskDelayUntil(&xLastWakeTime, xFrequency); // 100Hz
  }
}


void setup()
{
  Serial.begin(921600); 

  // Create a queue capable of holding 20 frames of data
  logQueue = xQueueCreate(20, sizeof(LogFrame));

  // Launch the Logging Task on Core 0, but with Priority 0 (Lowest)
  // Your BrainTask is Priority 1, so it will always interrupt the logger.
  xTaskCreatePinnedToCore(
    loggingTask,   
    "LogTask",     
    4000,          // Stack size 
    NULL,          
    0,             // Priority 0 (Background)
    NULL,          
    0              // Core 0
  );

  delay(1000); 

  // Initialize SPI encoder
  pend_encoder.initSPI();
  Serial.println("Pendulum Encoder Initialized.");
  encoder_cal(pend_encoder);

  // Initialize Button Pin
  pinMode(BUTTON_PIN, INPUT_PULLUP);
  Serial.println("Safety Button Initialized.");

  // Initialize BLDC encoder and Driver
  bldc_encoder.init();
  motor.linkSensor(&bldc_encoder);

  pcnt_counter_pause(PCNT_UNIT_0);
  pcnt_counter_clear(PCNT_UNIT_0);
  pcnt_event_enable(PCNT_UNIT_0, PCNT_EVT_H_LIM);
  pcnt_counter_resume(PCNT_UNIT_0);

  driver.voltage_power_supply = 20;
  driver.init();
  motor.linkDriver(&driver);

  // Controller Configuration
  motor.phase_resistance = 5.55;
  motor.current_limit = 1.5;
  motor.voltage_limit = 20;   
  motor.velocity_index_search = 3;

  // Current Sense Link
  current_sense.linkDriver(&driver);
  current_sense.init();
  motor.linkCurrentSense(&current_sense);

  // FOC Current Settings
  motor.torque_controller = TorqueControlType::foc_current; 
  motor.controller = MotionControlType::torque;

  // Initialize & Align
  motor.init();
  motor.initFOC(); 
  Serial.println("Motor Ready!");

  // Create Core 0 Task
  xTaskCreatePinnedToCore(
    core0_task,    // Function to implment task
    "BrainTask",  // Name of task
    10000,        // Stack size of task
    NULL,         // Task input parameter
    1,            // Priority of the task
    NULL,         // Task handle
    0             // Core where task runs
  );

  Serial.println("Dual-Core RTOS Started");
}

void loop()
{
  bldc_encoder.update();
  motor.loopFOC();

  // If estopped apply 0 torque
  if( is_estopped )
  {
    motor.target = 0.0f;
  }
  else
  {
    motor.target = shared_target_current;
  }
  motor.move();
}

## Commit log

2026-04-12 Added furuta pendulum MuJoCo sim files
    [12mm_rod_link.STL, 8mm_rod_link.STL, base_link.STL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]
2026-04-14 Added sensor for MuJoCo sim
2026-04-24 Updated pendulum meshes
    [12mm_rod_link.STL, 8mm_rod_link.STL, base_link.STL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]
2026-04-24 Temporarily moved old meshes and xml files to separate directory. Will remove later
    [12mm_rod_link.STL, 8mm_rod_link.STL, base_link.STL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]
2026-04-24 Added real hardware measurements to tun simulated XML model
    [drop_test_data.csv, rotor_test_data.csv]
2026-04-25 Removed unused legacy files
    [12mm_rod_link.STL, 8mm_rod_link.STL, base_link.STL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]
2026-04-25 Added arduino sketch for running model on hardware
2026-04-26 Restructured repository
    [drop_test_data.csv, rotor_test_data.csv]
2026-05-05 Add Solidworks assembly
2026-05-05 Update motor torque constant
2026-05-06 Added Solidworks assembly

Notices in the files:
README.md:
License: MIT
